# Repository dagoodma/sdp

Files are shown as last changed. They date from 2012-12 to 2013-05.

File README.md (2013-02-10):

                                                                          
         .oo          o                                                   
        .P 8          8                                                   
       .P  8 o    o  o8P .oPYo. odYo. .oPYo. ooYoYo. .oPYo. o    o .oPYo. 
      oPooo8 8    8   8  8    8 8' `8 8    8 8' 8  8 8    8 8    8 Yb..   
     .P    8 8    8   8  8    8 8   8 8    8 8  8  8 8    8 8    8   'Yb. 
    .P     8 `YooP'   8  `YooP' 8   8 `YooP' 8  8  8 `YooP' `YooP' `YooP' 
    ..:::::..:.....:::..::.....:..::..:.....:..:..:..:.....::.....::.....:
    ::::::::::::::::::::::::::::::::::::::::::::::::::::::::::::::::::::::
    ::::::::::::::::::::::::::::::::::::::::::::::::::::::::::::::::::::::
    
           o      o  d'b                                        8 
           8         8                                          8 
           8     o8 o8P  .oPYo. .oPYo. o    o .oPYo. oPYo. .oPYo8 
           8      8  8   8oooo8 8    8 8    8 .oooo8 8  `' 8    8 
           8      8  8   8.     8    8 8    8 8    8 8     8    8 
           8oooo  8  8   `Yooo' `YooP8 `YooP' `YooP8 8     `YooP' 
     ............:..:..:::.....::....8 :.....::.....:..:::::.....::.....::.
    ::::::::::::::::::::::::::::::ooP'.:::::::::::::::::::::::::::::::::::
    ::::::::::::::::::::::::::::::...:::::::::::::::::::::::::::::::::::'

Autonomous Lifeguard -- Senior Design Project for UCSC

*   Website: http://lifeguardrobotics.com
*   Source: https://github.com/dagoodma/sdp
*   Mailing list: [Google Groups](https://groups.google.com/a/ucsc.edu/forum/#!forum/albs-group)

This project consists of an autonomous surface vessel to aid a drowning
individual in the critical minutes that it takes a lifeguard to make it
out to a person. 

### License ###

The Autonomous Lifeguard project is proposed to be protected under either LGPL or GPLv3+.
See the *COPYING* file for more info.

### Credits ###

&copy; 2012-2013 [David Goodman](mailto:dagoodma@ucsc.edu),
 [Darrel Deo](mailto:ddeo@ucsc.edu),
 [Shehadeh Dajani](mailto:sdajani@ucsc.edu),
 [John Ash](mailto:jash@ucsc.edu)

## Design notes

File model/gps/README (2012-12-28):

Install drivers for FTDI, UART USB-Serial:
    http://www.ftdichip.com/FTDrivers.htm

Plug GPS devices in one at a time and record port names (*nix) or numbers
(windows) for each device. Enter these values into the portnums section
for each device in gps_autoconf.m

Run gps_autoconf.m is matlab. You will see:
    Connected to Locosys
    Connected to Mediatek
    Connected to Ublox
    Connected to San_Jose
    Connected to Sirf_Star

Use fscanf n matlab to print messages from a device. Locosys for example:
    > out = fscanf(ports{locosys})
    out =
    GGA,000525.836,,,,,0,0,,,M,,M,,*47
    > out = fscanf(ports{locosys})
    out =
    ...
    $GPRMC,000525.836,V,,,,,0.00,0.00,060180,,,N*4D
    $PMTK001,220,3*30
    $PMTK001,314,3*36
    $GPGGA,000526.836,,,,,0,0,,,M,,M,
    $GPRMC,000542.836,V,,,,,0.00,0.00,060180,,,N*4C
    $GPGGA,000527.836,,,,,0,0,,,M,,M,,*45
    $GPRMC,000527.836,V,,,,,0.00,0.00,060180,,,N*4F
    $GPGGA,000528.836,,,,,0,0,,,M,,M,,*4A

    Note that the above results were obtains when running the scripts indoors.

Verify timestamps at 1 Hz. See Messages for an explaination.

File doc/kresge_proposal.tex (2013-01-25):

 \documentclass[11pt]{article}
\usepackage[pdftex]{graphicx}
\usepackage{siunitx}
\usepackage{verbatim}
\usepackage{float}
\usepackage{lastpage}
\usepackage{fancyhdr}
\usepackage[margin=1in, paperwidth=8.5in, paperheight=11in]{geometry}
%\usepackage{indentfirst}

\newcommand{\HRule}{\rule{\linewidth}{0.5mm}}

% Header and Footer
\pagestyle{fancy}
%\fancyhead{} % clear all header fields
%\rhead{\vspace*{1em}\headone{David Goodman}\\
%	$118$ Hainline Road $\bullet$ Aptos, CA 95003\\
%	Phone: 714.363.1280\\
%	E-Mail: dagoodma@gmail.com}
%\cfoot{}

\renewcommand{\headrulewidth}{0pt}
%\renewcommand{\footrulewidth}{0.4pt}
%\cfoot{}
%\rfoot{Goodman \thepage}

\begin{document}

\begin{titlepage}
\begin{center}

% Upper part of the page. The '~' is needed because \\
% only works if a paragraph has started.
%\includegraphics[width=0.15\textwidth]{./logo}~\\[1cm]
\ \\[5.6cm]
\textsc{\LARGE \textbf{University of California, Santa Cruz} \\Baskin School of Engineering}\\[1.5cm]

\textsc{\Large Senior Design Project}\\[0.5cm]

% Title
\HRule \\[0.4cm]
{ \huge \bfseries Autonomous Lifeguard}\\[0.4cm]

\HRule \\[1.5cm]

% Author and supervisor
\begin{minipage}{0.4\textwidth}
\begin{flushleft} \large
\emph{Authors:}\\
Darrel \textsc{Deo}\\
David \textsc{Goodman}\\
John \textsc{Ash}\\
Shehadeh \textsc{Dajani}
\end{flushleft}
\end{minipage}
\begin{minipage}{0.4\textwidth}
\begin{flushright} \large
\emph{Advisors:} \\
Ph.D. ~Gabriel \textsc{Elkaim}\\
Ph.D. ~John \textsc{Vesecky}\\
Ph.D. ~Stephen \textsc{Petersen}
\end{flushright}
\end{minipage}

\vfill

% Bottom of the page
{\large \today}

\end{center}
\end{titlepage}

\section*{Abstract}
In the United States, there have been a reported 99 people that have drowned in the past year alone, with a good number of them occurring while a lifeguard was on duty. In that year, there were 63,000 individual cases where Lifeguards rescued people at risk of drowning. We are proposing an autonomous surface vehicle to aid and assist these drowning individuals during the critical minutes before help can reach them.\\

Our project allows a lifeguard to quickly target a drowning person with a magnifying scope that will obtain their GPS coordinates and communicate them to a boat located in the water beyond the shore break. The boat will autonomously navigate to the person, allowing them to hang on and stay afloat until the lifeguard arrives. This project aims to keep beaches safer by reducing the risk of drowning. 

\section*{Narrative}

\subsection*{Background}
The city of Los Angeles has employed the use of a device named EMILY (Emergency Integrated Lifesaving Lanyard) on their state beaches to save drowning victims. The device is deployed from the shore and remotely controlled by a human operator. Although it offers a degree of assistance, there exist multiple drawbacks to the system as a whole. The first is that it requires an operator, meaning that a lifeguard will be occupied with controlling the device during a rescue. The second is that the device must fight against the waves in order to reach the victim. This implies an unpredictable delay when navigating to the victim. The third drawback is that the device is limited by the field of view and skill of the operator.\\

We propose a fully autonomous system that will navigate to the location of a drowning victim, offering assistance as a lifeguard is deployed from shore. This eliminates the need for a human operator, allowing the lifeguard to swim out to the victim as the device navigates to the victim. The device will be stationed within the water at a certain distance from the shore and beyond the wave breaks so that it may arrive at a drowning victim's location swiftly.

\subsection*{Objective}

Motivated by the number of drowning cases each year, The Autonomous Lifeguard Senior Design Group aims to develop an assistive, life-preserving, vessel with the capability of navigating to and locating drowning individuals in open water. This vessel, the Autonomous Lifeguard Assistant (AtLAs), will be stationed in the open water on a beach or in a lake. The AtLAs will be coupled with an onshore control tower, the Command Post Acquisition System (ComPAS), that transmits the GPS coordinates of drowning individuals that have been spotted by a lifeguard. While the lifeguard swims to the drowning individual, the AtLAs will use its triple motor propulsion system to arrive at the victim's location at least three times as fast as a lifeguard can. Furthermore, the entire Autonomous Lifeguard System is designed to be a useful and affordable product for the public. The ultimate goal is to create a practical and superior aquatic life-saving system.

\subsection*{Procedure}
This project is composed of two systems, a command center (ComPAS) and Autonomous Lifeguard Assistant (AtLAs), which will communicate with each other over a wireless protocol. The ComPAS consists of a GPS-equipped scope mounted on a lifeguard post. When the lifeguard sees someone who is drowning, he or she will spot them through the scope and press a button. At that instant, the coordinate location of the victim will be obtained--through triangulation algorithms and a global coordinate system provided by the GPS--and sent to the AtLAs in the water. The AtLAs will then begin to self navigate to the location using its own on-board GPS device as well as an array of sensors for detecting the person. Upon reaching this destination, the AtLAs will intelligently traverse the area until it finds the drowning victim. The AtLAs will support the victim and allow them to rest while the lifeguard makes their way out.\\

In order to accomplish our objective, we propose a three phase approach: design, integration, and testing. In the design stage, which we are currently in, a majority of the research was accomplished to establish a solution to the task and physical and mathematical models were created to allow for an enlightened analysis of the proposed solution. Next, the models established in the design phase are to be rigorously examined in the testing phase to acquire real data to prove the accuracy and robustness of the model. Lastly, the integration stage, in which the minimum specifications will be addressed, involves assembling the final product by combining all the refined modules into a physical implementation that meets the specifications. These three phases encompass the life of the project. \\

Since mid-November, our team has made significant progress in completing the research and design phase for our project. We began by doing extensive background research related to the sensors and actuators, as well as the basic physical capabilities required. This led to modeling and physical calculation related to the buoyancy, hydrodynamics, motors, power budget, sensor specifications, and the accuracy of our navigation system. Using this research, we formulated various initial solutions, and then, with the input of trusted and qualified mentors, proceeded to amend, revise, and ultimately converge onto an effective solution. Next, we completed a group charter, an itemized budget, a Gantt chart, a project proposal, and have already given two presentations to audiences composed of engineering professors and students. In order to complete the design stage, we are in the process of designing physical prototypes of the ComPAS and the AtLAs and have already ordered and received a majority of the sensors we will be using. This first stage is nearly complete, and once we are done we will be ready to integrate our prototypes into a cohesive product.\\

The next phase is integration. In the integration phase, we will be combining the working prototypes from the design phase into a complete product. This will involve finalizing the ComPAS and improving its robustness for transportation to the test location. The AtLAs will also need to be assembled and finalized, outfitted with buoyancy foam and protective boat fenders, and cleared for use in lakes and oceans. Also, we will need to reinforce both the AtLAs and the ComPAS and ensure that they are properly waterproofed and protected against the elements. Once the integration of our systems is complete, we can begin testing and assessing the performance of the systems.\\

The testing phase is the third and final stage. It includes a thorough investigation of our assembled systems and their ability to meet the established objectives. Unit tests have been created that will help streamline this process and prevent fixes from being introduced that adversely affect another piece of the system without being detected. As a final test, we will place the ComPAS on the shore of a lake or beach in Santa Cruz, deploy the AtLAs from the water, and then use the ComPAS and AtLAs to save a "drowning" volunteer. Once our system passes this minimum specification we will have completed our project.

\subsection*{Qualifications}

Darrel Deo is our team leader. He will also be working on integrating the sensors and building the tripod, which will be used to obtain the GPS coordinates of the drowning victim. Darrel is qualified for this position because of his work at MIT. While at MIT, Darrel worked with the Robotics, Vision, and Sensor Networks Group (RVSN) where he helped develop an assistive device for the visually impaired. This experience makes him well qualified for leading our team, and handling the sensor integration for the project.\\

Shehadeh Dajani is managing our budget. He will also be leading our Printed Circuit Board (PCB) design and layout, along with our vehicle design. Shehadeh is qualified for these positions because he has taken a course on PCB design and designed numerous PCBs both educationally and industrially. Shehadeh has also had previous experience with ROVs, at the University of Maryland. Finally, Shehadeh will be heading the human detection portion of the project by working with Darrel to design and modify existing sensors for aquatic human detection.\\

John Ash is managing our schedule for the project. He will also be working on the wireless protocols, water proofing, and PCB fabrication. John is qualified for these positions because of his previous experience with point-to-point communications. His experience with the autonomous solar boat on campus in the Autonomous Systems Lab (ASL) makes him an excellent consultant for protecting our hardware from water. Furthermore, John has hands-on experience fabricating PCBs.\\

David Goodman is our document administrator. He will also be developing the Finite State Machine (FSM) for our robot and the navigation system. David is more than qualified for this position, because he has five years of software engineering experience in industry. He is able to oversee design and testing of the software portion of our project. David has also worked in the ASL on the boat project, and with a graduate student on GPS-related research for the lab. David has the necessary experience to head the design and implementation of the software navigation system for our project.

\subsection*{Benefits}

This project will directly benefit the Santa Cruz community, as well as any coastal community around the world, by assisting a lifeguard to be more effective at saving people from drowning. Furthermore, the target budget for the Autonomous Lifeguard System, including research, is aimed at making this project a sensible and affordable end product that has the real opportunity to be used. The project is established in a way to allow for expansion from the original scope so that the AtLAs can be used for search and rescue or patrolling situations. Overall, we plan on using our engineering skills and talents to design a product with the sole purpose of saving lives and reducing the risk of drowning across the globe.

\end{document}

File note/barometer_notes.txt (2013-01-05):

Barometric Pressure Sensor - BMP085 Breakout (sparkfun)
https://www.sparkfun.com/products/9694

digital pressure sensor by Bosch
range: +9000m .. -500m above sea level
features: temperature, I2C, calibrated, MSL 1

piezo resistive sensor
data: pressure (16-19 bits), temp. (16 bits)

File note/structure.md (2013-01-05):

Repository Structure
====================

* _doc_ - Documentation, datasheets, schematics, and images.
* _include_ - Header files for project source code.
* _model_ - MATLAB models and data.
* _note_ - Notes, guides, tutorials, research.
* _src_ - C source code files.
* _t_ - Unit tests and harnesses.
* _tool_ - Tools and utilities.
* _example_ - Example code.

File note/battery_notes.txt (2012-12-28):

LiPo RC battery pack voltages
--
3.7 volt battery = 1 cell x 3.7 volts (1S)
7.4 volt battery = 2 cells x 3.7 volts (2S)
11.1 volt battery = 3 cells x 3.7 volts (3S)
14.8 volt battery = 4 cells x 3.7 volts (4S)
18.5 volt battery = 5 cells x 3.7 volts (5S)
22.2 volt battery = 6 cells x 3.7 volts (6S)
29.6 volt battery = 8 cells x 3.7 volts (8S)
37.0 volt battery = 10 cells x 3.7 volts (10S)
44.4 volt battery = 12 cells x 3.7 volts (12S)

http://www.rchelicopterfun.com/rc-lipo-batteries.html

http://www.hobbyking.com/hobbyking/store/__14616__Turnigy_nano_tech_5000mah_6S_45_90C_Lipo_Pack.html

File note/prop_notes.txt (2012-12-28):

Notes:
--
Rule of thumb: 2" pitch = 400 RPM

Definitions:
--

Pitch: theoretical distance the prop travels on each rotation. This is theoretical because water is not a solid medium and the prop slips. 10 to 30% is normal, the lower numbers are found only on hi-performance props, specially prepared. 

Transom = stern = rear = aft-most 

http://www.modelpowerboat.com/content.php?152-RC-Model-Boat-Propellers

http://boatpropellers.iboats.com/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

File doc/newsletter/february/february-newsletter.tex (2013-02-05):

%%% LaTeX Template: Newsletter
%%%
%%% Source: http://www.howtotex.com/
%%% Feel free to distribute this template, but please keep the referal to HowToTeX.com.
%%% Date: September 2011

%%% ---------------
%%% PREAMBLE
%%% ---------------
\documentclass[10pt,a4paper]{article}

% Define geometry (without using the geometry package)
\setlength\topmargin{-48pt}
\setlength\headheight{0pt}
\setlength\headsep{25pt}
\setlength\marginparwidth{-20pt}
\setlength\textwidth{7.0in}
\setlength\textheight{9.5in}
\setlength\oddsidemargin{-30pt}
\setlength\evensidemargin{-30pt}

\frenchspacing						% better looking spacing

% Call packages we'll need
\usepackage[english]{babel}			% english
\usepackage{graphicx}				% images
\usepackage{amssymb,amsmath}		% math
\usepackage{multicol}				% three-column layout
\usepackage{url}					% clickable links
\usepackage{marvosym}				% symbols
\usepackage{wrapfig}				% wrapping text around figures
\usepackage[T1]{fontenc}			% font encoding
\usepackage{charter} 				% Charter font for main content
\usepackage{blindtext}				% dummy text
\usepackage{datetime}				% custom date
	\newdateformat{mydate}{\monthname[\THEMONTH] \THEYEAR}
\usepackage[pdfpagemode=FullScreen,
			colorlinks=false]{hyperref}	% links and pdf behaviour

% Customize (header and) footer
\usepackage{fancyhdr}
\pagestyle{fancy}
\lfoot{	\footnotesize 
		Newletter from LifeguardRobotics.com \\
		\Mundus\ \href{http://www.lifeguardrobotics.com}{LifeguardRobotics.com}	\quad
		\Telefon\ (831) 704-6771										\quad
		\Letter\ \href{mailto:lifeguardrobotics@gmail.com}{lifeguardrobotics@gmail.com}
	  }
\cfoot{}
\rfoot{\footnotesize ~\\ Page \thepage}
\renewcommand{\headrulewidth}{0.0pt}	% no bar on top of page
\renewcommand{\footrulewidth}{0.4pt}	% bar on bottom of page

%%% ---------------
%%% DEFINITIONS
%%% ---------------

% Define separators
\newcommand{\HorRule}[1]{\noindent\rule{\linewidth}{#1}} % Creating a horizontal rule
\newcommand{\SepRule}{\noindent							 % Creating a separator
						\begin{center}
							\rule{250pt}{1pt}
						\end{center}
						}						

% Define Title en News input
\newcommand{\JournalName}[1]{%
		\begin{center}	
			%\Huge \usefont{T1}{augie}{m}{n}
			\Huge \usefont{T1}{cmr}{m}{n}
			%\huge \bfseries 
			#1%
		\end{center}	
		\par \normalsize \normalfont}
		
\newcommand{\JournalIssue}[1]{%
		\hfill \textsc{\mydate \today, No #1}
		\par \normalsize \normalfont}

\newcommand{\NewsItem}[1]{%
		\usefont{T1}{augie}{m}{n} 	
		\large #1 \vspace{4pt}
		\par \normalsize \normalfont}
		
\newcommand{\NewsAuthor}[1]{%
			\hfill by \textsc{#1} \vspace{4pt}
			\par \normalfont}		

%%% ---------------
%%% BEGIN DOCUMENT
%%% ---------------
\begin{document}
% Title	
% -----
\JournalIssue{1}
\JournalName{The Autonomous Lifeguard Project}
\noindent\HorRule{3pt} \\[-0.75\baselineskip]
\HorRule{1pt}
% -----

% Front article
% -----
\vspace{0.5cm}
	\SepRule
\vspace{0.5cm}

\begin{center}
\begin{minipage}[h]{0.80\linewidth}
	\begin{wrapfigure}{l}{0.415\textwidth}
		{%
		\setlength{\fboxsep}{0pt}%
		\setlength{\fboxrule}{1pt}%
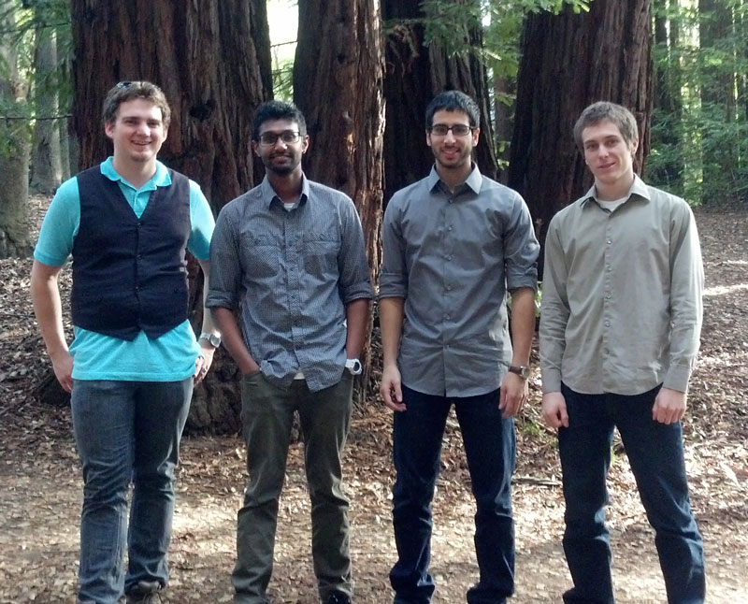
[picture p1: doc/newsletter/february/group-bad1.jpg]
		\fbox{}%
		}%
		%\\	% this spacer is needed to make the text on the right fit OK
	\end{wrapfigure}
	
	\NewsItem{Who Are We}
	\emph{We are a group of UC Santa Cruz computer and robotics engineering students who are building a robot to assist lifeguards in saving drowning individuals on beaches, at sea, and in other bodies of water. In the United States, there has been a reported 99 people that have drowned in the past year alone, with a good number of them occurring while a lifeguard was on duty. We propose an autonomous boat that can navigate to a person, allowing them to hang on and stay a float until the lifeguard arrives. Our aim is to keep beaches safer by reducing the risk of drowning.}
\end{minipage}
\end{center}
% -----

% Other news (1)
% -----
\vspace{0.5cm}
	\SepRule
\vspace{0.5cm}
\begin{multicols}{3}
	\NewsItem{Progress}
	\NewsAuthor{D. Goodman}
	January has been a very productive month for our team. We are making substantial progress on the project. Throughout January, we have been hard at work writing, researching, coding, and soldering. Administratively, we have completed a Gantt chart, a website, and have entered into the Texas Instruments Analog Design Contest. In the hardware portion, we have purchased a boat and begun to modify it with new motors, electronic speed controllers, and batteries.  The command center---an encoded tripod assembly that the lifeguard will use to designate a drowning person---is coming together as well. We have acquired a tripod and absolute rotary encoders for triangulation. The encoder housing has been created, and a software interface is now in the works to take angular measurements and translate them into distance. Great care has been taken to ensure that the encoders are very precise so that we can triangulate the position of a drowning person accurately with minimal error. Many of our other sensors are nearly complete as well. We have an accelerometer up and running, our thermal imagining nearly complete, our altimeter is working, our GPSs running and we are analyzing their data in MATLAB, and we have been planning our approach to implementing the microwave radar and sonar sensors after inspecting their analog waveforms with an oscilloscope. 
\begin{center}
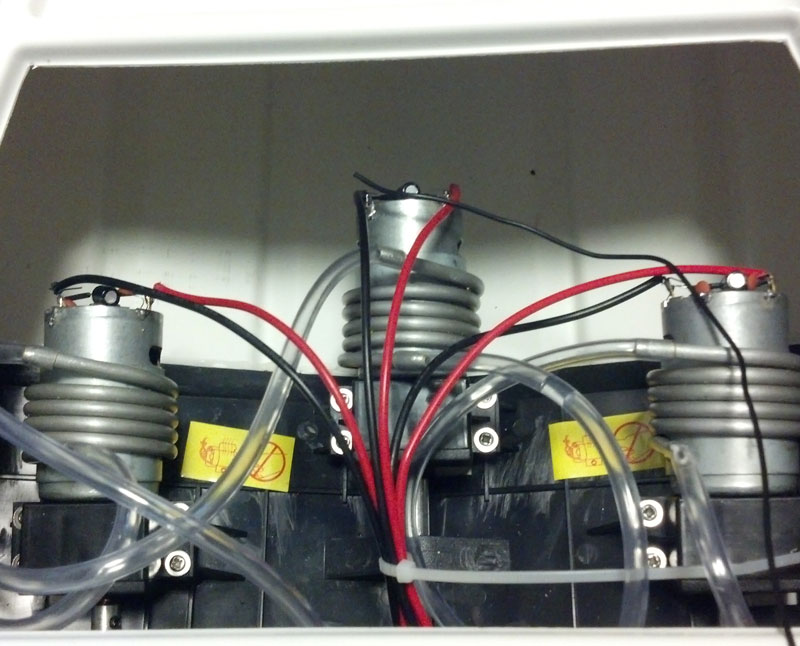
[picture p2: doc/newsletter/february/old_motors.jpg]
			
		\end{center}
Overall, this past month has been productive on all fronts and the team is anxious to continue with work in February.
		
% -----

\vspace{1cm}
% Other news (2)
% -----
\NewsItem{Direction}
\NewsAuthor{D. Deo}
	Every week, the team specifies a minimum set of personal goals that they wish to complete.
 This week the group will focus on modeling accurate data from the encoders, XBee, GPS, and thermal sensor. The goal is to get the encoders to read accurate angles and have the ability to be calibrated to a zero degree point within software. Data from the GPS and XBee need to be obtained over a duration of time to analyze and correct for any error that may be present. The thermal sensor data is to be mapped to an RGB array so that heat signatures may be seen in real time. These sensors and modules are the last that need be implemented before the integration phase where the various components will be mounted on their respective subsystem. Comprehensive testing will occur after each sensor is up and running. We will also begin designing hierarchical finite state machines for the boat and the command center. These will provide our systems with the intelligence to act autonomously and make decisions on its own. So far, we are ahead of schedule for February.

% -----
%\columnbreak
\vspace{1cm}
% Other news (2)
% -----
\NewsItem{Support}
\NewsAuthor{D. Deo}
The Autonomous Lifeguard Group is moving quite swiftly and is hopeful that the next phases of the project will yield exceptional results. As a devoted team, we are currently funding the project entirely ourselves. Optimistic about the future of the Autonomous Lifeguard Project, we would appreciate any form of support that would help the project advance. Donations are welcome and can be submitted via our website. All considerations will be recognized by the team.
\end{multicols}
% -----
\end{document}

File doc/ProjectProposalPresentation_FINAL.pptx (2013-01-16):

## Autonomous Lifeguard

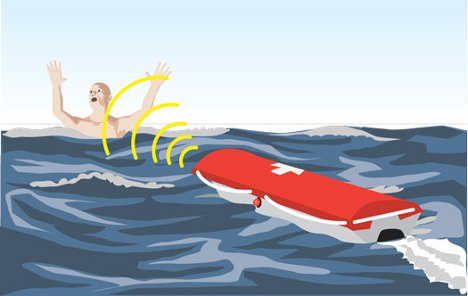
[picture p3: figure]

- Darrel R. Deo (Project Lead)
- Shehadeh H. Dajani
- John P. Ash
- David A. Goodman
- University of California at Santa Cruz

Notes: Hello, We are the autonomous Lifeguard group, My name is …, I am a … year … Engineer. Hello my name is ...... I am a ..... with a focus in ......

## Mission Statement

- Autonomous surface vessel (ASV) to aid and assist drowning victims.
- 2-part system:
  - Command Center
  - ASV

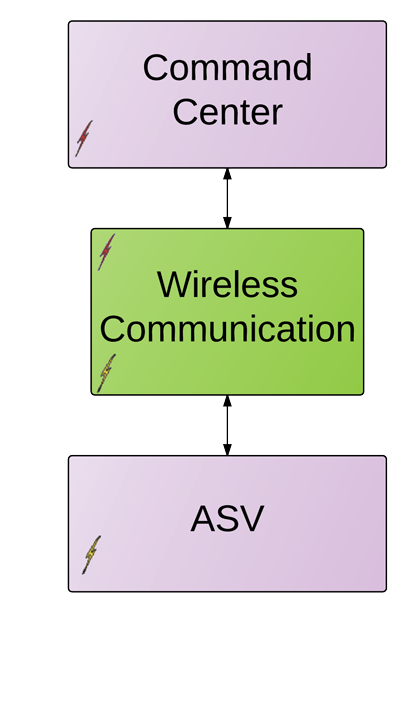
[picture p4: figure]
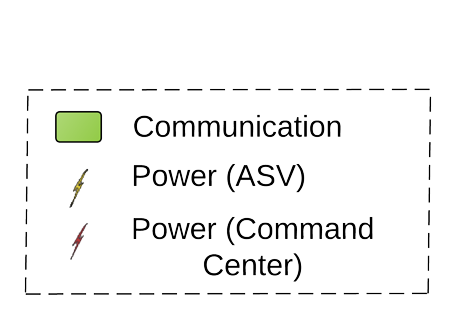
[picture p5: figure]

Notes: We are proposing an autonomous surface vehicle to aid a drowning individual in the critical minutes that it takes a lifeguard to make it out to a person.

We are interested in the case beyond the breaks where it would take a lifeguard a while to make it out to the person.

Our system is composed of two subsystems

## Motivation

- Santa Cruz - “Surf City”
- E.M.I.L.Y - Emergency Integrated Lifesaving Lanyard
      - Remote controlled
      - Deployed from beach
      - Non-practical

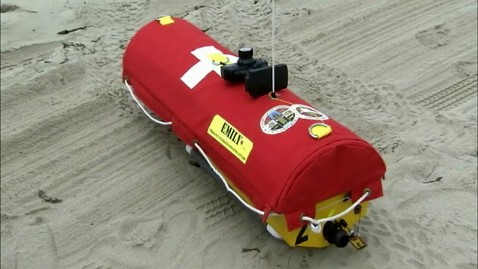
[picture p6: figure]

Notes: range is

## Objective

Develop a system that will aid drowning victims.

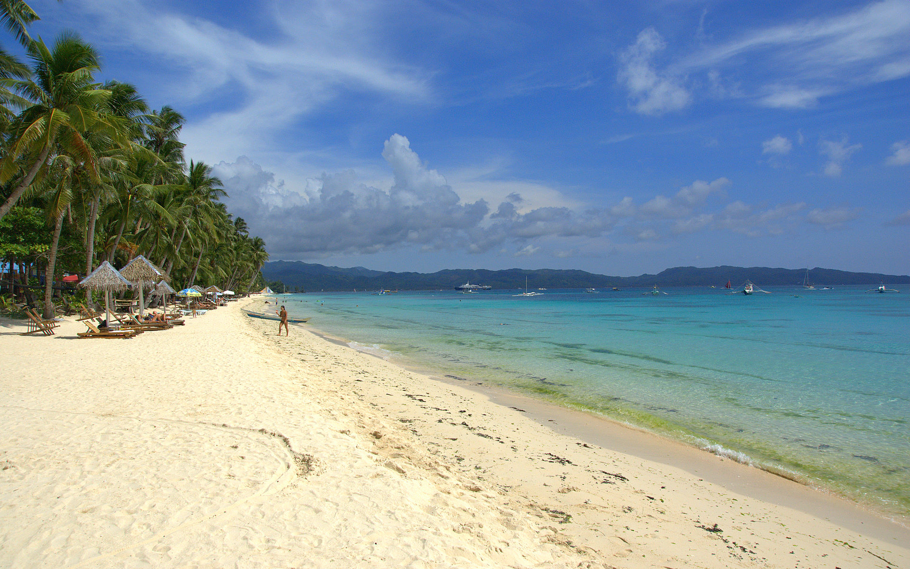
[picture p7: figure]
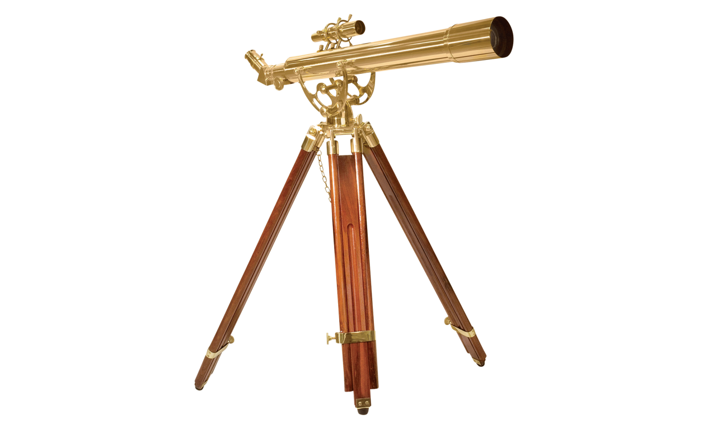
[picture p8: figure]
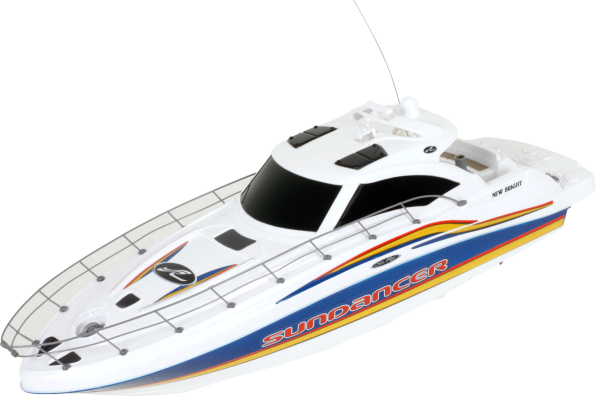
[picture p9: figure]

## Scope of Specifications

  - Range of rescue will be from beyond surf breaks to 600ft.
  - ASV will be anchored at a specified waypoint in the water.
  - Command Center will be located on a lifeguard post.
  - Both subsystems will communicate via wireless protocol.

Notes: Range: It will take the average swimmer to swim up to 600 ft, at which point a lifeguard will be able to swim out in 5 minutes.

## Minimum Functionality

- Command Center
  - Obtain the drowning victim’s location within +/- 50 ft.
  - Required to send wireless information at least 600 ft.
  - Must have an override remote control function allowing full control of ASV.

## Minimum Functionality

- Autonomous Surface Vehicle:
  - Speed of ASV must, at least, double that of a lifeguard’s swim speed (3.7 MPH).
  - Batteries must last for at least 12 hours without recharge.
  - Must be able to navigate to a specified GPS coordinate within +/- 20 ft.

## Differential GPS

- Calibrate reference station position average over time
- Calculate instantaneous GPS error
- Transmit error to rover for corrections
- 1.1cm to 3.2ft of accuracy achieved

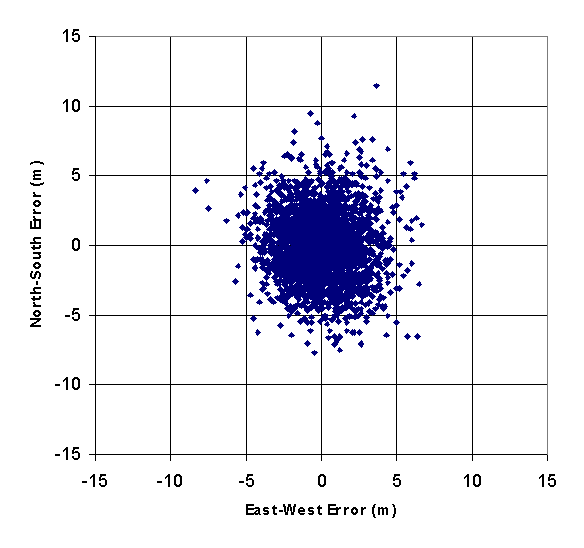
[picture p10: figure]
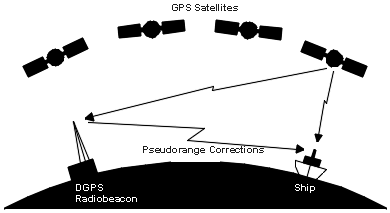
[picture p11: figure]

## Encoder Accuracy

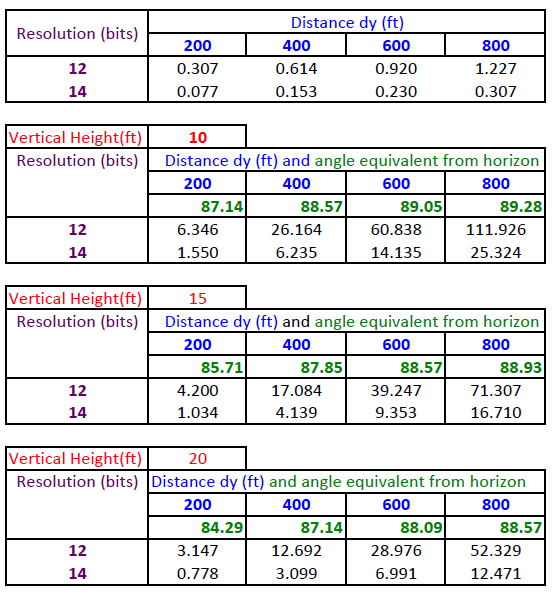
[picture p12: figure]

## Block Diagram

- Command Center

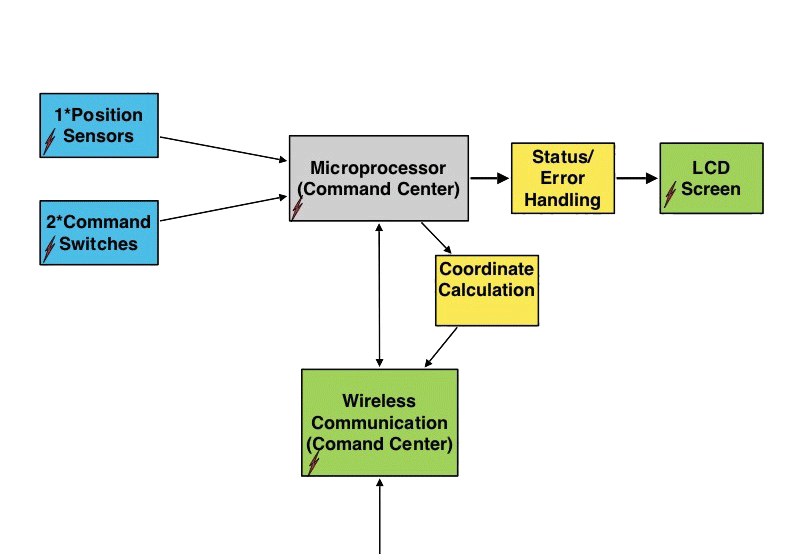
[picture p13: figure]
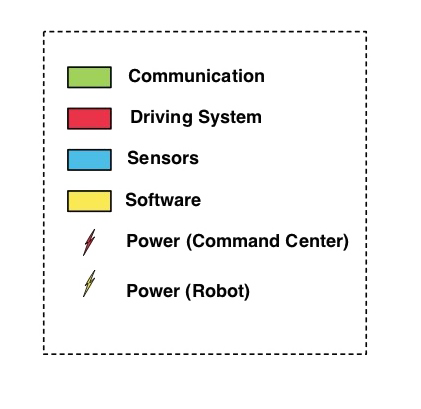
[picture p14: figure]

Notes: Add sensor blocks
Switches can be put into interface sensors

## Block Diagram

- ASV

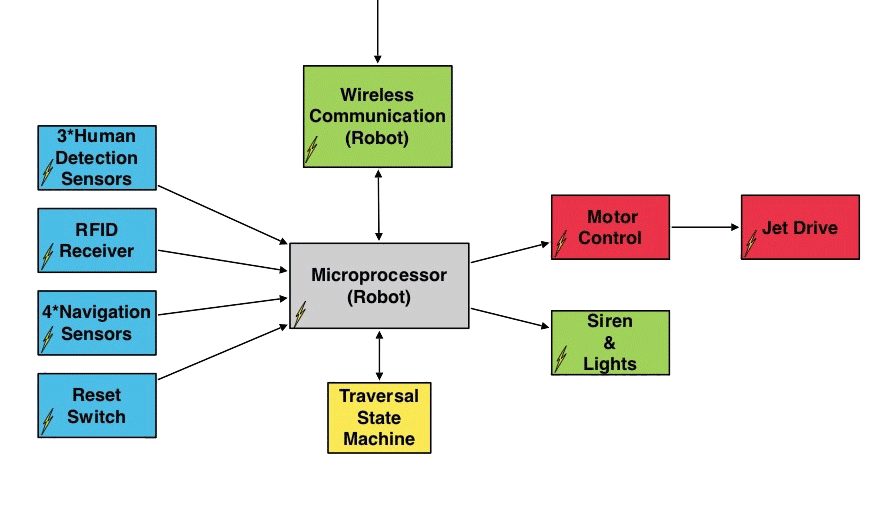
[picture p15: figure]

## Division of Labor

- John Ash – Schedule Planner
      - Wireless Protocol, Power Management, PCB Routing
- Shehadeh Dajani – Budget Coordinator
      - Motor Control, PCB Design/Layout, Vehicle Design
- Darrel Deo – Team Leader
      - Sensor Integration, Tripod Design, Modeling
- David Goodman - Document Administrator
      - Software Test Harnesses, FSM Design, GPS Integration

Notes: John: qualifications: XBee experience (121 expansion), autonomous boat for ASL,
David: software eng. for 5yrs industry exp., DSP, and GPS (ASL)
Shehadeh: Quals: Mechatronics motor control, solidworks fiend, board layout exp.
Darrel : Quals: Sensor Technology experience, math modeling--Solid Mechanics

## Gantt Chart

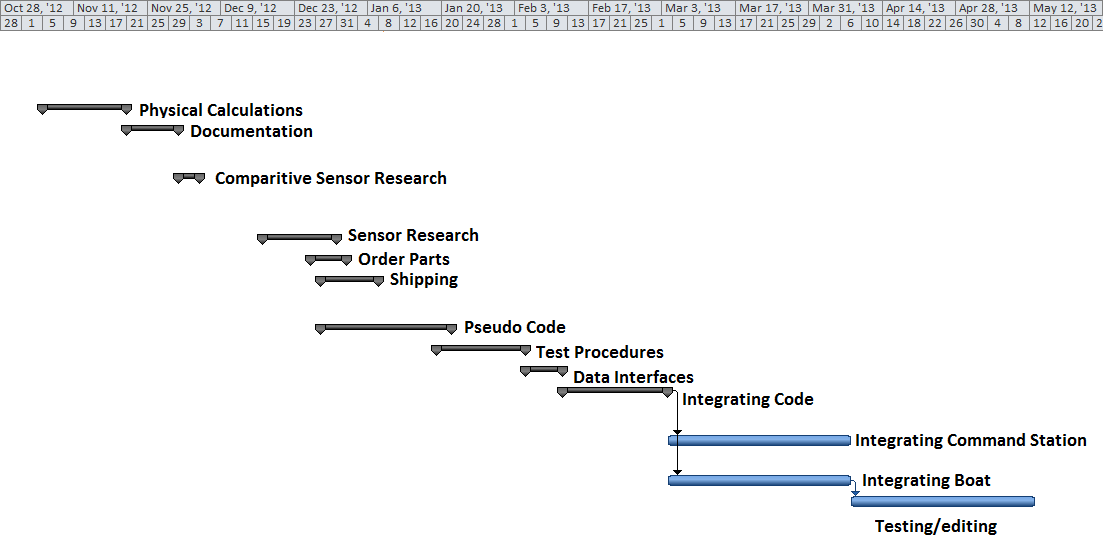
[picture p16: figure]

## Itemized Budget

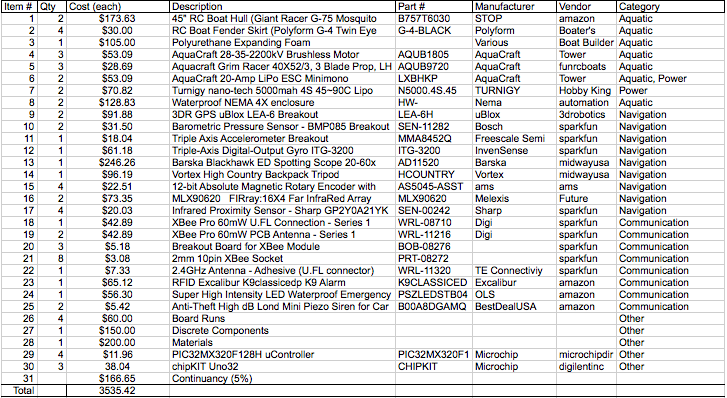
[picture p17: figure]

## Progress

- Boat Hull has been ordered and is in route.
- Started extracting coordinate data from GPS devices.
- Established Xbee communication.
- Beginning to interface decoder wheels with Micro.
- Currently seeking funding sources (Kresge, Oakes, Crown, and Corporations.)

## Conclusion

- All team members are proficient in their field of responsibility.
- Gabriel Elkaim has shown support and offered mentorship.
- We have access to field testing environments (e.g. pool, lake, ocean).
- This project has the real potential to be an asset to lifeguards and save lives.
- Marketable to beaches across the country.

## References

- EMILY:
  - http://www.popsci.com/gadgets/article/2010-06/invention-month-robot-lifeguard

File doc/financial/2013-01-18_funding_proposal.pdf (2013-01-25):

## University of California, Santa Cruz

Baskin School of Engineering

Senior Design Project

# Autonomous Lifeguard

Authors:
Darrel Deo
David Goodman
John Ash
Shehadeh Dajani

Advisors:
Ph.D. Gabriel Elkaim
Ph.D. John Vesecky
Ph.D. Stephen Petersen

January 18, 2013

## Abstract

In the United States, there have been a reported 99 people that have drowned in the past year alone, with a good number of them occurring while a lifeguard was on duty. In that year, there were 63,000 individual cases where Lifeguards rescued people at risk of drowning. We are proposing an autonomous surface vehicle to aid and assist these drowning individuals during the critical minutes before help can reach them.

Our project allows a lifeguard to quickly target a drowning person with a magnifying scope that will obtain their GPS coordinates and communicate them to a boat located in the water beyond the shore break. The boat will autonomously navigate to the person, allowing them to hang on and stay afloat until the lifeguard arrives. This project aims to keep beaches safer by reducing the risk of drowning.

## Narrative

Background

The city of Los Angeles has employed the use of a device named EMILY (Emergency Integrated Lifesaving Lanyard) on their state beaches to save drowning victims. The device is deployed from the shore and remotely controlled by a human operator. Although it offers a degree of assistance, there exist multiple drawbacks to the system as a whole. The first is that it requires an operator, meaning that a lifeguard will be occupied with controlling the device during a rescue. The second is that the device must fight against the waves in order to reach the victim. This implies an unpredictable delay when navigating to the victim. The third drawback is that the device is limited by the field of view and skill of the operator.

We propose a fully autonomous system that will navigate to the location of a drowning victim, offering assistance as a lifeguard is deployed from shore. This eliminates the need for a human operator, allowing the lifeguard to swim out to the victim as the device navigates to the victim. The device will be stationed within the water at a certain distance from the shore and beyond the wave breaks so that it may arrive at a drowning victim’s location swiftly.

Objective

Motivated by the number of drowning cases each year, The Autonomous Lifeguard Senior Design Group aims to develop an assistive, life-preserving, vessel with the capability of navigating to and locating drowning individuals in open water. This vessel, the Autonomous Lifeguard Assistant (AtLAs), will be stationed in the open water on a beach or in a lake. The AtLAs will be coupled with an onshore control tower, the Command Post Acquisition System (ComPAS), that transmits the GPS coordinates of drowning individuals that have been spotted by a lifeguard. While the lifeguard swims to the drowning individual, the AtLAs will use its triple motor propulsion system to arrive at the victim’s location at least three times as fast as a lifeguard can. Furthermore, the entire Autonomous Lifeguard System is designed to be a useful and affordable product for the public. The ultimate goal is to create a practical and superior aquatic life-saving system.

Procedure

This project is composed of two systems, a command center (ComPAS) and Autonomous Lifeguard Assistant (AtLAs), which will communicate with each other over a wireless protocol. The ComPAS consists of a GPS-equipped scope mounted on a lifeguard post. When the lifeguard sees someone who is drowning, he or she will spot them through the scope and press a button. At that instant, the coordinate location of the victim will be obtained–through triangulation algorithms and a global coordinate system provided by the GPS–and sent to the AtLAs in the water. The AtLAs will then begin to self navigate to the location using its own on-board GPS device as well as an array of sensors for detecting the person. Upon reaching this destination, the AtLAs will intelligently traverse the area until it finds the drowning victim. The AtLAs will support the victim and allow them to rest while the lifeguard makes their way out.

In order to accomplish our objective, we propose a three phase approach: design, integration, and testing. In the design stage, which we are currently in, a majority of the research was accomplished to establish a solution to the task and physical and mathematical models were created to allow for an enlightened analysis of the proposed solution. Next, the models established in the design phase are to be rigorously examined in the testing phase to acquire real data to prove the accuracy and robustness of the model. Lastly, the integration stage, in which the minimum specifications will be addressed, involves assembling the final product by combining all the refined modules into a physical implementation that meets the specifications. These three phases encompass the life of the project.

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

The next phase is integration. In the integration phase, we will be combining the working prototypes from the design phase into a complete product. This will involve finalizing the ComPAS and improving its robustness for transportation to the test location. The AtLAs will also need to be assembled and finalized, outfitted with buoyancy foam and protective boat fenders, and cleared for use in lakes and oceans. Also, we will need to reinforce both the AtLAs and the ComPAS and ensure that they are properly waterproofed and protected against the elements. Once the integration of our systems is complete, we can begin testing and assessing the performance of the systems.

The testing phase is the third and final stage. It includes a thorough investigation of our assembled systems and their ability to meet the established objectives. Unit tests have been created that will help streamline this process and prevent fixes from being introduced that adversely affect another piece of the system without being detected. As a final test, we will place the ComPAS on the shore of a lake or beach in Santa Cruz, deploy the AtLAs from the water, and then use the ComPAS and AtLAs to save a ”drowning” volunteer. Once our system passes this minimum specification we will have completed our project.

Qualifications

Darrel Deo is our team leader. He will also be working on integrating the sensors and building the tripod, which will be used to obtain the GPS coordinates of the drowning victim. Darrel is qualified for this position because of his work at MIT. While at MIT, Darrel worked with the Robotics, Vision, and Sensor Networks Group (RVSN) where he helped develop an assistive device for the visually impaired. This experience makes him well qualified for leading our team, and handling the sensor integration for the project.

Shehadeh Dajani is managing our budget. He will also be leading our Printed Circuit Board (PCB) design and layout, along with our vehicle design. Shehadeh is qualified for these positions because he has taken a course on PCB design and designed numerous PCBs both educationally and industrially. Shehadeh has also had previous experience with ROVs, at the University of Maryland. Finally, Shehadeh will be heading the human detection portion of the project by working with Darrel to design and modify existing sensors for aquatic human detection.

John Ash is managing our schedule for the project. He will also be working on the wireless protocols, water proofing, and PCB fabrication. John is qualified for these positions because of his previous experience with point-to-point communications. His experience with the autonomous solar boat on campus in the Autonomous Systems Lab (ASL) makes him an excellent consultant for protecting our hardware from water. Furthermore, John has hands-on experience fabricating PCBs.

David Goodman is our document administrator. He will also be developing the Finite State Machine (FSM) for our robot and the navigation system. David is more than qualified for this position, because he has five years of software engineering experience in industry. He is able to oversee design and testing of the software portion of our project. David has also worked in the ASL on the boat project, and with a graduate student on GPS-related research for the lab. David has the necessary experience to head the design and implementation of the software navigation system for our project.

Benefits

This project will directly benefit the Santa Cruz community, as well as any coastal community around the world, by assisting a lifeguard to be more effective at saving people from drowning. Furthermore, the target budget for the Autonomous Lifeguard System, including research, is aimed at making this project a sensible and affordable end product that has the real opportunity to be used. The project is established in a way to allow for expansion from the original scope so that the AtLAs can be used for search and rescue or patrolling situations. Overall, we plan on using our engineering skills and talents to design a product with the sole purpose of saving lives and reducing the risk of drowning across the globe.

## Autonomous Lifeguard Project

### Itemized Budget

Item # | Qty | Cost (each) | Description | Part # | Manufactu rer | Vendor | Category | Notes
1 | 2 | $173.63 | 45" RC Boat Hull (Giant Racer G-75 Mosquito Craft) | B757T6030 | STOP | amazon | Aquatic | Going to test, then possibly modify or return.
2 | 4 | $30.00 | RC Boat Fender Skirt (Polyform G-4 Twin Eye Fender 6.5 x 23 - Black w/Air Adapter) | G-4-BLACK | Polyform | Boater's Marine Supply | Aquatic
3 | 1 | $105.00 | Polyurethane Expanding Foam (2 gal kit 50/50 mix) | | Various | Boat Builder Central | Aquatic | 480 lbs of buoyancy U.S. Coast Guard Approved
4 | 3 | $53.09 | AquaCraft 28-35-2200kV Brushless Motor MiniMono | AQUB1805 | AquaCraft | Tower Hobbies | Aquatic
5 | 3 | $28.69 | Aquacraft Grim Racer 40X52/3, 3 Blade Prop, LH | AQUB9720 | AquaCraft | funrcboats | Aquatic | 40mm (1.57") x 52MM Pitch. Copper-Beryllium-Titanium. Must hand finish.
6 | 2 | $53.09 | AquaCraft 20-Amp LiPo ESC Minimono | LXBHKP | AquaCraft | Tower Hobbies | Aquatic, Power | 20 Amp
7 | 2 | $70.82 | Turnigy nano-tech 5000mah 4S 45~90C Lipo Battery Pack | N5000.4S.45 | TURNIGY | Hobby King | Power | 5000mAh, 4 Cell (14.8V), 45C Constant / 90C Burst
8 | 2 | $128.83 | Waterproof NEMA 4X enclosure | HW-J161406SC | Nema | automatio ndirect | Aquatic | 4SCREWS OPQ CVR GRY 4X 16X14X6IN
9 | 2 | $91.88 | 3DR GPS uBlox LEA-6 Breakout | LEA-6H | uBlox | 3drobotics | Navigation | UART, USB interfaces. Includes ceramic antenna, LNA, SAW filter, and 3.3V batt.
10 | 2 | $31.50 | Barometric Pressure Sensor - BMP085 Breakout | SEN-11282 | Bosch | sparkfun | Navigation | I2C interface. Piezoelectric, includes temp. sensor.
11 | 1 | $18.04 | Triple Axis Accelerometer Breakout | MMA8452Q | Freescale Semi | sparkfun | Navigation | I2C interface. 3-axis, 2 ISR pins, optional HPF.
12 | 1 | $61.18 | Triple-Axis Digital-Output Gyro ITG-3200 Breakout | ITG-3200 | InvenSens e | sparkfun | Navigation | I2C interface. 3-axis, optional LPF, and ISR pin.
13 | 1 | $246.26 | Barska Blackhawk ED Spotting Scope 20-60x 60mm Angled Body | AD11520 | Barska | midwayus a | Navigation | Great at 600-800ft. 60mm, 20-60x.
14 | 1 | $96.19 | Vortex High Country Backpack Tripod | HCOUNTRY | Vortex | midwayus a | Navigation | Full size, 4.48 ft tall, 2.1 lbs.
15 | 4 | $22.51 | 12-bit Absolute Magnetic Rotary Encoder with SSI and PWM Output incl. Diagnostic Functions | AS5045-ASST | ams | ams | Navigation | Absolute position sensing with 0.09 deg resolution.
16 | 2 | $73.35 | MLX90620 FIRray:16X4 Far InfraRed Array | MLX90620 | Melexis | Future Electronics | Navigation | I2C interface. ~23 ft range.

1 1/17/2013 12:46 PM

## Autonomous Lifeguard Project

### Itemized Budget

Item # | Qty | Cost (each) | Description | Part # | Manufactu rer | Vendor | Category | Notes
17 | 4 | $20.03 | Infrared Proximity Sensor - Sharp GP2Y0A21YK | SEN-00242 | Sharp | sparkfun | Navigation | 2.6 ft.
18 | 1 | $42.89 | XBee Pro 60mW U.FL Connection - Series 1 (802.15.4) | WRL-08710 | Digi | sparkfun | Communi cation | UART interface. External antenna, 1 mi range, 250 kbps max
19 | 2 | $42.89 | XBee Pro 60mW PCB Antenna - Series 1 (802.15.4) | WRL-11216 | Digi | sparkfun | Communi cation | UART interface. PCB antenna, 1 mi range, 250 kbps max
20 | 3 | $5.18 | Breakout Board for XBee Module | BOB-08276 | | sparkfun | Communi cation | Convert to standard pin spacing.
21 | 8 | $3.08 | 2mm 10pin XBee Socket | PRT-08272 | | sparkfun | Communi cation | XBee standoffs for breakout board.
22 | 1 | $7.33 | 2.4GHz Antenna -Adhesive (U.FL connector) | WRL-11320 | TE Connectivi y | sparkfun | Communi cation | 2.4 GHz, 2 dB gain
23 | 1 | $65.12 | RFID Excalibur K9classicedp K9 Alarm | K9CLASSIC EDP | Excalibur | amazon | Communi cation | Returns rover to base waypoint. Shah tested 50 ft range.
24 | 1 | $56.30 | Super High Intensity LED Waterproof Emergency Strobe Light (BLUE/RED) | PSZLEDSTB 0421-BR | OLS | amazon | Communi cation | 12V/24V: 100mA -660mA/50mA - 330mA
25 | 2 | $5.42 | Anti-Theft High dB Lond Mini Piezo Siren for Car Alarm | B00A8DGA MQ | BestDeal USA | amazon | Communi cation | 12V DC, 150mA/90V DC, 90mA, waterproof
26 | 4 | $60.00 | Board Runs | | | | Other
27 | 1 | $150.00 | Discrete Components | | | | Other
28 | 1 | $200.00 | Materials | | | | Other | Steel, coating, acrylic, wood, MDF, foam
29 | 4 | $11.96 | PIC32MX320F128H uController | PIC32MX320 F128H | Microchip | microchipd irect | Other | 80 MHz, 16 KB RAM, 2 I2C/SPI/UART, 16 A/D, 5 timer/PWM, 2 comp., 53 I/O
30 | 3 | 38.04 | chipKIT Uno32 | CHIPKIT UNO32 | Microchip | digilentinc | Other | PIC32MX320F128 for prototyping.
31 | | $166.65 | Continuancy (5%) | | | | | Cushion for unforseen events such as additional parts and rush delivery.
Total | | 3535.42

2 1/17/2013 12:46 PM

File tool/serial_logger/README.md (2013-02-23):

# Serial Logger #

*   Website: http://lifeguardrobotics.com
*   Source: https://github.com/dagoodma/sdp/tree/master/tool/serial\_logger
*   Mailing list: [Google Groups](https://groups.google.com/a/ucsc.edu/forum/#!forum/alg-group)

This tool is used to connect to a device over serial and send and receive data while logging the interaction to a file.

## Usage ##

When run, the tool will list available serial ports and query the user to select one for connecting to. Once connected, the tool will display and record and data recieved. (TODO: Add the ability to send data.)

Follow the three steps below to use the serial logger. If you would like to use the GUI, follow step 1 from *With GUI*, and if you prefer the command line, follow step 1 from *Without GUI*. Steps 2 and 3 are the same for either method.

1. Run the tool.
    - For the GUI, on *Windows* run `serial_logger.exe`, on Mac run `serial_logger.app`.
    - Without GUI, open a terminal in `serial_logger/src`, then run `python serial_logger.py`. See _Arguments_ under the *Configuring*  section below for more information.

2. Choose serial port.
    - Windows devices are numbered ie. *COM4*
    - Mac are mounted with a serial number to the */dev* folder ie. */dev/tty.usbserial-A1012WFD*

3. Done.
    - Incoming serial data will be displayed in the console window.
    - Open *serial_logger.log* to view the recorded session.

## Configuring ##

The serial logger can be configured by setting desired parameters in *serial_logger/src/.config.cfg*. If you are using the command line, arguments may be passed which will override the config. See *Arguments* below for more details.

### Arguments ###

    python serial_logger.py -h | [-l log_file] [--loglevel=level] [-c config_file] [ -t timeout] [-b baud_rate] [device_path]

#### Positional ####
    device_path           device path or id of the serial port

#### Optional ####

    -b BAUD_RATE, --baud BAUD_RATE
                        baud rate for the serial connection (default: 9600)

    -c CONFIG_FILE, --config CONFIG_FILE
                        config file with default values (default: .config.cfg)

    -t TIMEOUT, --timeout TIMEOUT
                        serial connection timeout in seconds (default: 5)

    -l LOG_FILE, --log LOG_FILE
                        log file to record session to (default:
                        serial_logger.log)

    --loglevel {DEBUG,INFO,WARNING,ERROR,CRITICAL}
                        sets the logging level (default: INFO)

    -h, --help          show this help message and exit

## Compatibility ##

This module was written for Python 2.7.3, and has been tested on Windows 7 (64 and 32 bit), and Mac OS X ??.

TODO: Add python 3.3 support.

## Author ##

&copy; 2012-2013 David Goodman

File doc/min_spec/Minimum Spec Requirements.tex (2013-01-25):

\documentclass[11pt]{amsart}
\usepackage{geometry, color, mathtools, amsfonts, graphics,amsmath}                % See geometry.pdf to learn the layout options. There are lots.
\geometry{letterpaper}                   % ... or a4paper or a5paper or ... 
%\geometry{landscape}                % Activate for for rotated page geometry
\usepackage[parfill]{parskip}    % Activate to begin paragraphs with an empty line rather than an indent
\usepackage{graphicx}
\usepackage{amssymb}
\usepackage{epstopdf}
\DeclareGraphicsRule{.tif}{png}{.png}{`convert #1 `dirname #1`/`basename #1 .tif`.png}
\begin{document}

\title{Minimum Specification Requirements}

\author{Autonomous Lifeguard Group}
%\date{}                                           % Activate to display a given date or no date

\maketitle
{
In order to achieve a passing mark in the CMPE 129 Senior Design Series, a minimum specification must be met.
The Autonomous Lifeguard Group will be expected to demo the entire system in a body of water within a set scope of functionality. 

The demo will take place on a lake in Santa Cruz, where a waypoint will be selected by an advisor within the range of no more than 100 meters from the shoreline. A teammate will operate the Command Center obtaining GPS coordinates of the waypoint of interest. The Autonomous Surface Vessel (ASV) will be docked in the lake at a point no more than 300 meters away from the point of interest. It will be required to navigate to the waypoint within the amount of time it would take a lifeguard to swim to that point. This will be calculated with the formula below:

\section{Command Center}
The Command Center must offer ease-of-use to the operator by allowing for swift maneuverability and a push-button interface for commands and operation. It is to be mounted at a location on the shore at least 15 feet above water level. The Command Center must be able to obtain the latitudinal and longitudinal coordinates of the selected waypoint, and wirelessly communicate the coordinates to the ASV at a distance of at least 350 meters.

\section{Autonomous Surface Vessel}
The Autonomous Surface Vessel must be deployable from a location in the water within the above mentioned waypoint radius (300m from waypoint). In addition, the ASV must have enough buoyancy to support a person. The ASV must be able to wirelessly communicate with the Command Center at a distance of at least 350 meters. Finally, the ASV must be able to reach its target waypoint within the amount of time it would take a lifeguard to swim there.

}

\end{document}

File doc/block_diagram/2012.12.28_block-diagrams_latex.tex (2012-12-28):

\documentclass{article}
\usepackage[pdftex]{graphicx}
\usepackage{epstopdf}
\usepackage{amsmath, amssymb, calc}
\usepackage{mathtools}
\usepackage{siunitx}
\usepackage{verbatim}
\usepackage{caption}
\usepackage{float}
\usepackage{multirow}
\usepackage{caption}
\usepackage{subcaption}
\usepackage{enumerate}
\usepackage{steinmetz}
\usepackage{lastpage}
\usepackage{fancyhdr}

\pagestyle{fancy}
\lhead{Darrel Deo, Shehadah Dajani,\\ John Ash, David Goodman}
\rhead{Autonomous Lifeguard,\\ Fall 2012}
\chead{\thepage\ of \pageref{LastPage}}
\lfoot{Autonomous Lifeguard --- Block Diagram}
\cfoot{}
\renewcommand{\headrulewidth}{0.4pt}
\renewcommand{\footrulewidth}{0.4pt}

\newcommand*\sepline{%
  \begin{center}
    \rule[1ex]{.5\textwidth}{.5pt}
  \end{center}}

\usepackage{blindtext}
\begin{document} 

\begin{center}
{\bf \Large Autonomous Lifeguard\\
	Block Diagrams}
\end{center}

\begin{figure}[H]
		\begin{center}
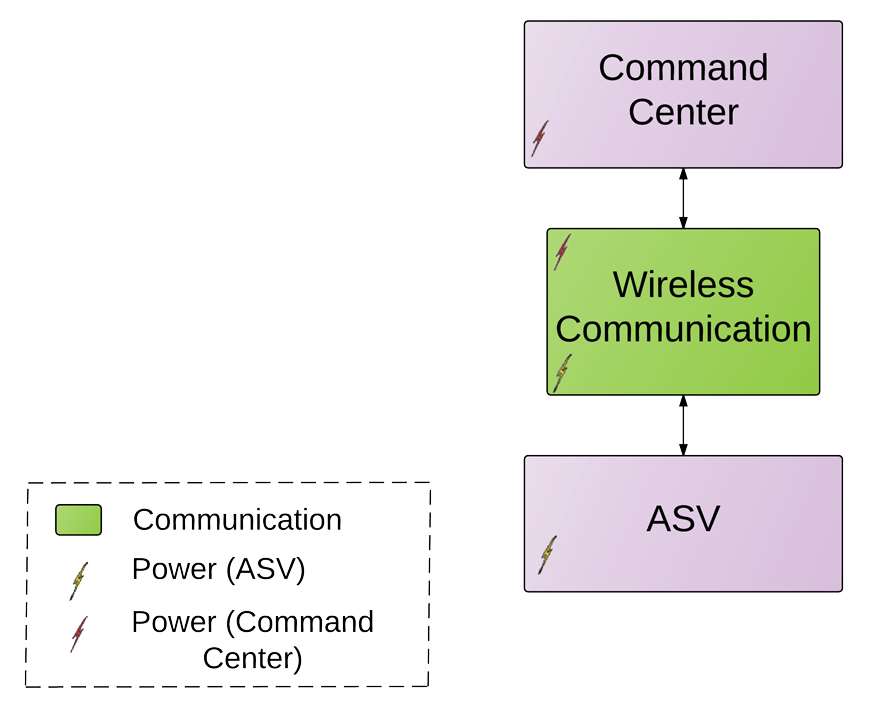
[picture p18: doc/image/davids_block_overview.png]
		\centerline{}
		\caption{System Overview}
		%\label{fig:1_freqz}
		\end{center}
	\end{figure}

\begin{figure}[H]
	\centering
\begin{subfigure}[b]{1\linewidth}		
	\begin{center}
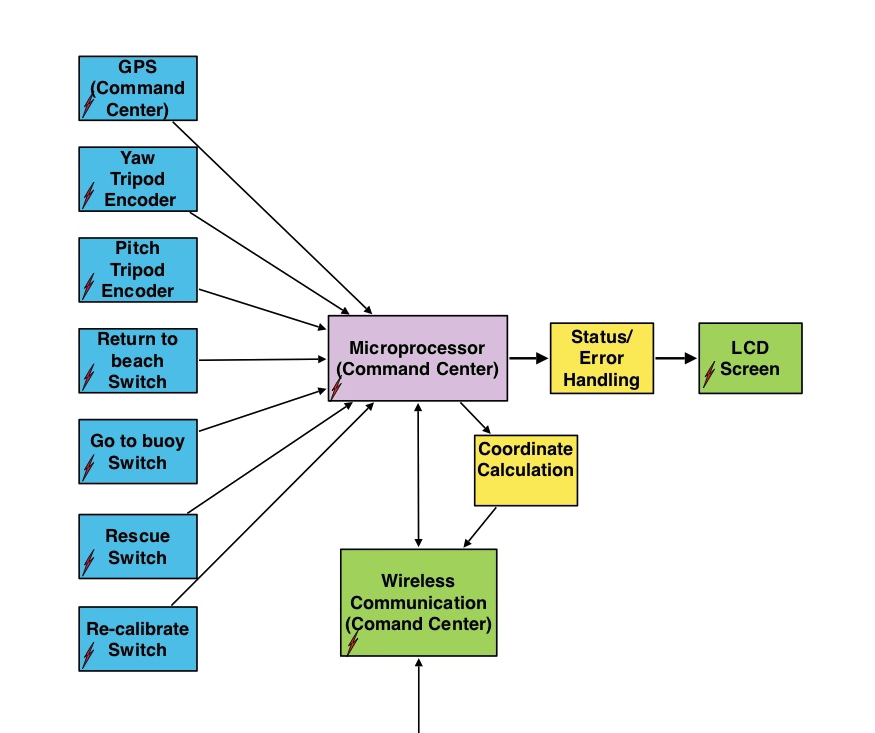
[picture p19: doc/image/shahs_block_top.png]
	\centerline{}
	%\caption{Schematic}
	%\label{fig:rgb_schem}
	\end{center}
\end{subfigure}
\begin{subfigure}[bH]{1\linewidth}
	\begin{center}
	\centerline{}
	%\caption{Specifications}
	%\label{fig:rgb_spec}
	\end{center}
	\end{subfigure}%
	\caption{Command Center Block Diagram}
	%\label{fig:connect4}
\end{figure}

\begin{figure}[H]
	\centering
\begin{subfigure}[b]{1\linewidth}		
	\begin{center}
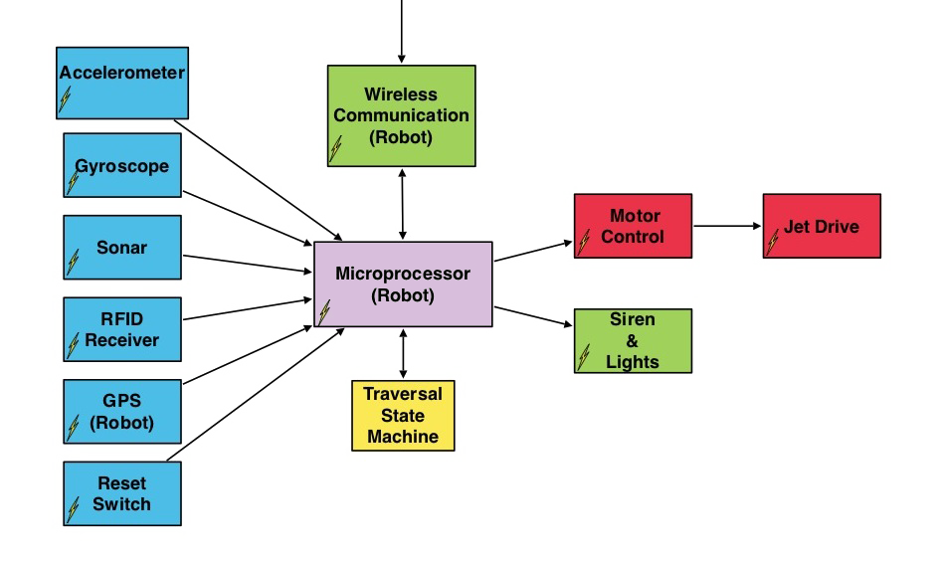
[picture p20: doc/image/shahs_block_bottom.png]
	\centerline{}
	%\caption{Schematic}
	%\label{fig:rgb_schem}
	\end{center}
\end{subfigure}
\begin{subfigure}[bH]{1\linewidth}
	\begin{center}
	\centerline{}
	%\caption{Specifications}
	%\label{fig:rgb_spec}
	\end{center}
	\end{subfigure}%
	\caption{ASV Block Diagram}
	%\label{fig:connect4}
\end{figure}

\end{document}

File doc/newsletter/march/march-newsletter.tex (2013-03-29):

%%% LaTeX Template: Newsletter
%%%
%%% Source: http://www.howtotex.com/
%%% Feel free to distribute this template, but please keep the referal to HowToTeX.com.
%%% Date: September 2011

%%% ---------------
%%% PREAMBLE
%%% ---------------
\documentclass[10pt,a4paper]{article}

% Define geometry (without using the geometry package)
\setlength\topmargin{-48pt}
\setlength\headheight{0pt}
\setlength\headsep{25pt}
\setlength\marginparwidth{-20pt}
\setlength\textwidth{7.0in}
\setlength\textheight{9.5in}
\setlength\oddsidemargin{-30pt}
\setlength\evensidemargin{-30pt}

\frenchspacing						% better looking spacing

% Call packages we'll need
\usepackage[english]{babel}			% english
\usepackage{graphicx}				% images
\usepackage{amssymb,amsmath}		% math
\usepackage{multicol}				% three-column layout
\usepackage{url}					% clickable links
\usepackage{marvosym}				% symbols
\usepackage{wrapfig}				% wrapping text around figures
\usepackage[T1]{fontenc}			% font encoding
\usepackage{charter} 				% Charter font for main content
\usepackage{blindtext}				% dummy text
\usepackage{datetime}				% custom date
\usepackage{caption}
	\newdateformat{mydate}{\monthname[\THEMONTH] \THEYEAR}
\usepackage[pdfpagemode=FullScreen,
			colorlinks=false]{hyperref}	% links and pdf behaviour

% Customize (header and) footer
\usepackage{fancyhdr}
\pagestyle{fancy}
\lfoot{	\footnotesize 
		Newletter from LifeguardRobotics.com \\
		\Mundus\ \href{http://www.lifeguardrobotics.com}{LifeguardRobotics.com}	\quad
		\Telefon\ (831) 704-6771										\quad
		\Letter\ \href{mailto:lifeguardrobotics@gmail.com}{lifeguardrobotics@gmail.com}
	  }
\cfoot{}
\rfoot{\footnotesize ~\\ Page \thepage}
\renewcommand{\headrulewidth}{0.0pt}	% no bar on top of page
\renewcommand{\footrulewidth}{0.4pt}	% bar on bottom of page

%%% ---------------
%%% DEFINITIONS
%%% ---------------

% Define separators
\newcommand{\HorRule}[1]{\noindent\rule{\linewidth}{#1}} % Creating a horizontal rule
\newcommand{\SepRule}{\noindent							 % Creating a separator
						\begin{center}
							\rule{250pt}{1pt}
						\end{center}
						}						

% Define Title en News input
\newcommand{\JournalName}[1]{%
		\begin{center}	
			\Huge \usefont{T1}{cmr}{m}{n}
			#1%
		\end{center}	
		\par \normalsize \normalfont}
		
\newcommand{\JournalIssue}[1]{%
        \hfill \textsc{\mydate \today, No #1}
        \par \normalsize \normalfont}

\newcommand{\NewsItem}[1]{%
		\usefont{T1}{augie}{m}{n} 	
		\large #1 \vspace{4pt}
		\par \normalsize \normalfont}
		
\newcommand{\NewsAuthor}[1]{%
			\hfill by \textsc{#1} \vspace{4pt}
			\par \normalfont}		

%%% ---------------
%%% BEGIN DOCUMENT
%%% ---------------
\begin{document}
% Title	
% -----
\JournalIssue{2}
\JournalName{The Autonomous Lifeguard Project}
\noindent\HorRule{3pt} \\[-0.75\baselineskip]
\HorRule{1pt}
% -----

% Front article
% -----
\vspace{0.5cm}
	\SepRule
\vspace{0.5cm}
\begin{center}
\begin{minipage}[h]{0.80\linewidth}
	\begin{wrapfigure}{l}{0.378\textwidth}
		{%
		\setlength{\fboxsep}{0pt}%
		\setlength{\fboxrule}{1pt}%
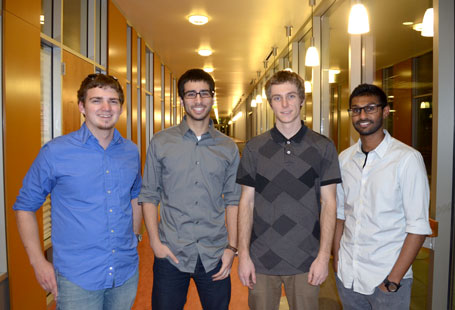
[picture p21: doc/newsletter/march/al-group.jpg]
		\fbox{}%
		\caption*{Left to right: J. Ash, S. Dajani, D. Goodman, D. Deo}
		}%
		%\\	% this spacer is needed to make the text on the right fit OK
	\end{wrapfigure}
	
	\NewsItem{Who Are We}
	\emph{We are a group of UC Santa Cruz computer and robotics engineering students who are building a robot to assist lifeguards in saving drowning individuals on beaches, at sea, and in other bodies of water. In the United States, there has been a reported 99 people that have drowned in the past year alone, with a good number of them occurring while a lifeguard was on duty. We propose an autonomous boat that can navigate to a person, allowing them to hang on and stay a float until the lifeguard arrives. Our aim is to keep beaches safer by reducing the risk of drowning.}
\end{minipage}
\end{center}
% -----

% 
% -----
\vspace{0.5cm}
	\SepRule
\vspace{0.5cm}
\begin{multicols}{3}
	\NewsItem{Milestones}
	\NewsAuthor{D. Goodman}
    
    We are all very pleased to announce that our command center is nearing completion. As March comes to an end, our project continues to grow and progress. Throughout this month, many hours were dedicated to implementing and integrating sensors, performing testing, and debugging the command center. Last week, we met our desired basic functionality for the command center, and created a video demonstrating its usage. A technical presentation was given before an audience of our peers that discussed our progress, challenges, and future plans.
\begin{center}
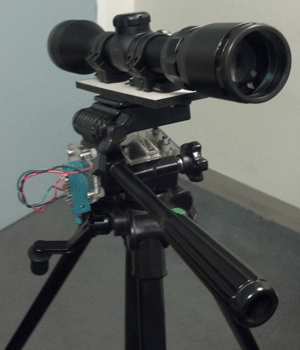
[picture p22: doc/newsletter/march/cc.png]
			
		\end{center}
The months of February and March have brought our team closer to reaching our goals. The completion of our boat is the next major milestone. We plan to accomplish this during April and May, so that by June we will have a working prototype. 
		
% -----

\vspace{1cm}
% Other news (2)
% -----
\NewsItem{Future Work}
\NewsAuthor{D. Goodman}
	Although the engineering buildings are very quiet during spring break, we are currently working hard to get the boat into the water. Shehadeh is working diligently to equip the boat with the new motors and emergency RC receiver. These modifications will allow us to reach a drowning victim quickly, and safely. Darrel, David, and John are busy implementing autonomous features into the boat, via a navigation and drive system. Our goal is to have the boat navigating on its own in the water by this coming weekend.

Following this weekend's testing, we will continue to work on the navigation system, and to get the command center talking to the boat from the shore. Once the boat is able to navigate to waypoints, we will begin the integration of our human detection sensor array, which includes sonar and thermal imaging. We are eager to continue making progress in every direction, and spring is proving to be very productive so far.

% -----
%\columnbreak
\vspace{1cm}
% Other news (2)
% -----
\NewsItem{Support}
\NewsAuthor{D. Deo}
The Autonomous Lifeguard Group would like to extend their utmost appreciation to those who have supported our cause. With the help of our donors, we have been able to partially fund our ambitious project. Done with the ComPAS, we will now focus our efforts on the AtLAs in hopes to complete our project within the coming months. We do ask that anyone interested in contributing to our project visit our team website and donate. All forms of support are welcome.
\end{multicols}
% -----
\end{document}

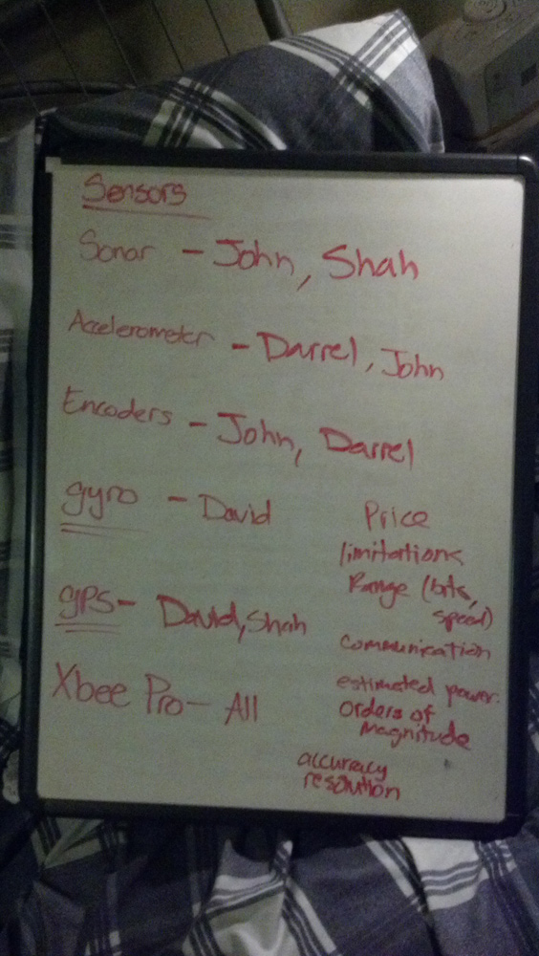
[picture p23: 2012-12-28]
doc/image/2012.09.20_sensor_assignments.jpg

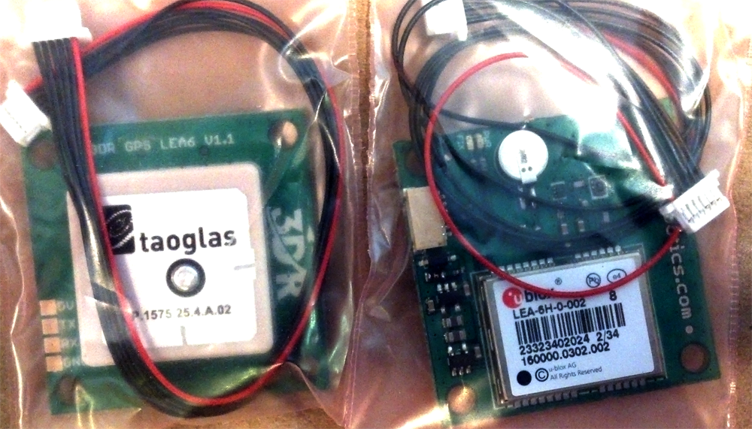
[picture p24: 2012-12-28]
doc/image/ublox_gpses.png

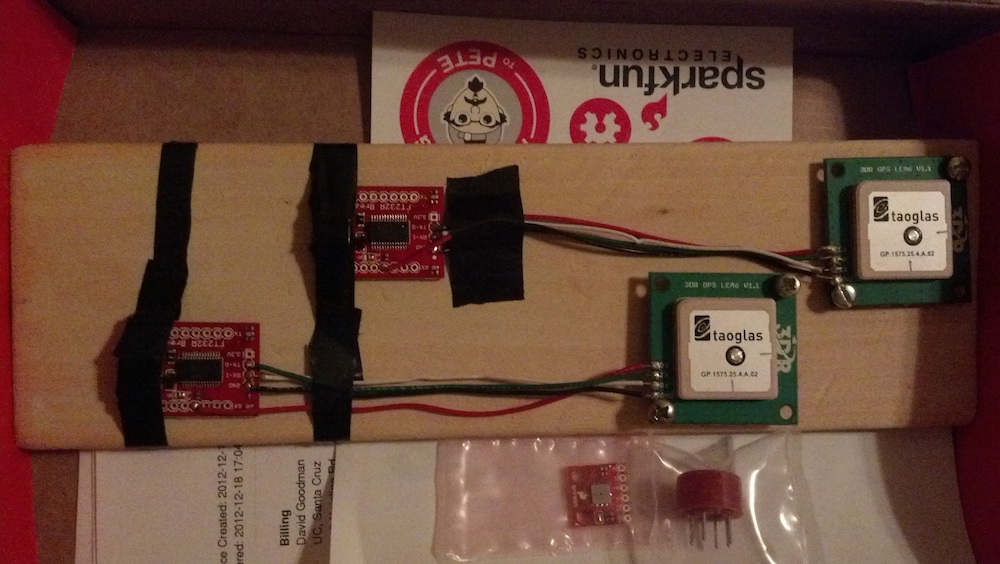
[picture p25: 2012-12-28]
doc/image/gps_proto_and_altimeter.jpg

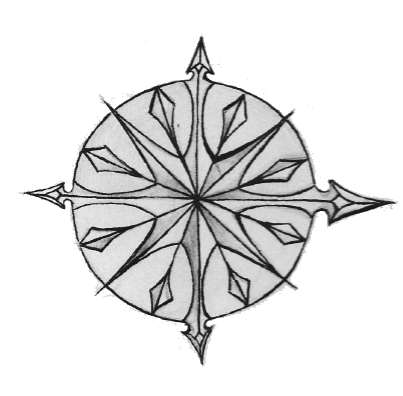
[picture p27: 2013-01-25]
doc/doxygen/api/html/compas.png

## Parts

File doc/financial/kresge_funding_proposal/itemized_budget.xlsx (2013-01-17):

Item # | Qty | Cost (each) | Description | Part # | Manufacturer | Vendor | Category | Notes | Link | Purchaser
1 | 2 | $173.63 | 45" RC Boat Hull (Giant Racer G-75 Mosquito Craft) | B757T6030 | STOP | amazon | Aquatic | Going to test, then possibly modify or return. | http://www.amazon.com/Mosquito-Racing-Electric-Control-Cooling/dp/B002F9TTBK | Shah
2 | 4 | $30.00 | RC Boat Fender Skirt (Polyform G-4 Twin Eye Fender 6.5 x 23 - Black w/Air Adapter) | G-4-BLACK | Polyform | Boater's Marine Supply | Aquatic |  | http://www.boatersmarinesupply.com/m7/36797--polyform-g-4-twin-eye-fender-6-5-x-23-black-w-air-adapter.html
3 | 1 | $105.00 | Polyurethane Expanding Foam (2 gal kit 50/50 mix) |  | Various | Boat Builder Central | Aquatic | 480 lbs of buoyancy U.S. Coast Guard Approved | http://boatbuildercentral.com/proddetail.php?prod=E_foam_2gal#.UKcDTpgR4nw
4 | 3 | $53.09 | AquaCraft 28-35-2200kV Brushless Motor MiniMono | AQUB1805 | AquaCraft | Tower Hobbies | Aquatic |  | http://www3.towerhobbies.com/cgi-bin/wti0001p?&I=LXBHKN&P=M
5 | 3 | $28.69 | Aquacraft Grim Racer 40X52/3, 3 Blade Prop, LH | AQUB9720 | AquaCraft | funrcboats | Aquatic | 40mm (1.57") x 52MM Pitch. Copper-Beryllium-Titanium. Must hand finish. | http://www.funrcboats.com/ProductInfo.aspx?productid=AQUB9720
6 | 2 | $53.09 | AquaCraft 20-Amp LiPo ESC Minimono | LXBHKP | AquaCraft | Tower Hobbies | Aquatic, Power | 20 Amp | http://www3.towerhobbies.com/cgi-bin/wti0001p?&I=LXBHKP&P=0
7 | 2 | $70.82 | Turnigy nano-tech 5000mah 4S 45~90C Lipo Battery Pack | N5000.4S.45 | TURNIGY | Hobby King | Power | 5000mAh, 4 Cell (14.8V), 45C Constant / 90C Burst | http://www.hobbyking.com/hobbyking/store/__11957__turnigy_nano_tech_5000mah_4s_45_90c_lipo_pack.html
8 | 2 | $128.83 | Waterproof NEMA 4X enclosure | HW-J161406SC | Nema | automationdirect | Aquatic | 4SCREWS OPQ CVR GRY 4X 16X14X6IN | http://www.automationdirect.com/adc/Shopping/Catalog/Enclosures/Non-Metal_(NEMA_4X_-a-_3R)/JIC_(6_in._X_4_in._to_20_in._X_16_in.)/HW-J161406SC
9 | 2 | $91.88 | 3DR GPS uBlox LEA-6 Breakout | LEA-6H | uBlox | 3drobotics | Navigation | UART, USB interfaces. Includes ceramic antenna, LNA, SAW filter, and 3.3V batt. | http://store.diydrones.com/3DR_GPS_LEA_6_p/br-3drlea-6.htm | David
10 | 2 | $31.50 | Barometric Pressure Sensor - BMP085 Breakout | SEN-11282 | Bosch | sparkfun | Navigation | I2C interface. Piezoelectric, includes temp. sensor. | https://www.sparkfun.com/products/9694 | David
11 | 1 | $18.04 | Triple Axis Accelerometer Breakout | MMA8452Q | Freescale Semi | sparkfun | Navigation | I2C interface. 3-axis, 2 ISR pins, optional HPF. | https://www.sparkfun.com/products/10955 | David
12 | 1 | $61.18 | Triple-Axis Digital-Output Gyro ITG-3200 Breakout | ITG-3200 | InvenSense | sparkfun | Navigation | I2C interface. 3-axis, optional LPF, and ISR pin. | https://www.sparkfun.com/products/9801
13 | 1 | $246.26 | Barska Blackhawk ED Spotting Scope 20-60x 60mm Angled Body | AD11520 | Barska | midwayusa | Navigation | Great at 600-800ft. 60mm, 20-60x. | http://www.midwayusa.com/product/766437/barska-blackhawk-ed-spotting-scope-20-60x-60mm-angled-body-with-tripod-and-hard-case-rubber-armored-black
14 | 1 | $96.19 | Vortex High Country Backpack Tripod | HCOUNTRY | Vortex | midwayusa | Navigation | Full size, 4.48 ft tall, 2.1 lbs. | http://www.midwayusa.com/product/623795/vortex-high-country-backpack-tripod
15 | 4 | $22.51 | 12-bit Absolute Magnetic Rotary Encoder with SSI and PWM Output incl. Diagnostic Functions | AS5045-ASST | ams | ams | Navigation | Absolute position sensing with 0.09 deg resolution. | http://www.ams.com/eng/Products/Magnetic-Position-Sensors/Magnetic-Rotary-Position-Sensors/AS5045/(oi)/1 | David sampled
16 | 2 | $73.35 | MLX90620 FIRray:16X4 Far InfraRed Array | MLX90620 | Melexis | Future Electronics | Navigation | I2C interface. ~23 ft range. | http://www.futureelectronics.com/en/Technologies/Product.aspx?ProductID=MLX90620ESFBAD000TUMELEXIS7020660&IM=0
17 | 4 | $20.03 | Infrared Proximity Sensor - Sharp GP2Y0A21YK | SEN-00242 | Sharp | sparkfun | Navigation | 2.6 ft. | https://www.sparkfun.com/products/242
18 | 1 | $42.89 | XBee Pro 60mW U.FL Connection - Series 1 (802.15.4) | WRL-08710 | Digi | sparkfun | Communication | UART interface. External antenna, 1 mi range, 250 kbps max | https://www.sparkfun.com/products/8710 | John
19 | 2 | $42.89 | XBee Pro 60mW PCB Antenna - Series 1 (802.15.4) | WRL-11216 | Digi | sparkfun | Communication | UART interface. PCB antenna, 1 mi range, 250 kbps max | https://www.sparkfun.com/products/11216 | John
20 | 3 | $5.18 | Breakout Board for XBee Module | BOB-08276 |  | sparkfun | Communication | Convert to standard pin spacing. | https://www.sparkfun.com/products/8276? | John
21 | 8 | $3.08 | 2mm 10pin XBee Socket | PRT-08272 |  | sparkfun | Communication | XBee standoffs for breakout board. | https://www.sparkfun.com/products/8272 | John
22 | 1 | $7.33 | 2.4GHz Antenna - Adhesive (U.FL connector) | WRL-11320 | TE Connectiviy | sparkfun | Communication | 2.4 GHz, 2 dB gain | https://www.sparkfun.com/products/11320 | John
23 | 1 | $65.12 | RFID Excalibur K9classicedp K9 Alarm | K9CLASSICEDP | Excalibur | amazon | Communication | Returns rover to base waypoint. Shah tested 50 ft range. | http://www.amazon.com/Excalibur-K9classicedp-Alarm-Interupt-Includ/dp/B003NGCTS4
24 | 1 | $56.30 | Super High Intensity LED Waterproof Emergency Strobe Light (BLUE/RED) | PSZLEDSTB0421-BR | OLS | amazon | Communication | 12V/24V: 100mA - 660mA/50mA - 330mA | http://www.amazon.com/gp/product/B009EFJBHK/ref=noref?ie=UTF8&psc=1&s=automotive
25 | 2 | $5.42 | Anti-Theft High dB Lond Mini Piezo Siren for Car Alarm | B00A8DGAMQ | BestDealUSA | amazon | Communication | 12V DC, 150mA/90V DC, 90mA, waterproof | http://www.amazon.com/BestDealUSA-Anti-Theft-Piezo-Siren-Alarm/dp/B00A8DGAMQ
26 | 4 | $60.00 | Board Runs |  |  |  | Other
27 | 1 | $150.00 | Discrete Components |  |  |  | Other
28 | 1 | $200.00 | Materials |  |  |  | Other | Steel, coating, acrylic, wood, MDF, foam
29 | 4 | $11.96 | PIC32MX320F128H uController | PIC32MX320F128H | Microchip | microchipdirect | Other | 80 MHz, 16 KB RAM, 2 I2C/SPI/UART, 16 A/D, 5 timer/PWM, 2 comp., 53 I/O | http://www.microchipdirect.com/ProductSearch.aspx?keywords=PIC32MX320F128H | David sampled
30 | 3 | 38.04 | chipKIT Uno32 | CHIPKIT UNO32 | Microchip | digilentinc | Other | PIC32MX320F128 for prototyping. | http://www.digilentinc.com/Products/Detail.cfm?Prod=CHIPKIT-UNO32
31 |  | $166.65 | Continuancy (5%) |  |  |  |  | Cushion for unforseen events such as additional parts and rush delivery.
Total |  | 3535.42

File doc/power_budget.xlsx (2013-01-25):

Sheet: Atlas
Item # | Device | Power Source | Power Rails (V) |  |  | Supply Current (mA) |  | Power Consumption (mW)
 |  |  | Min | Typical | Max | Min | Max | Min | Max | Notes | Datasheet Link
1 | uBlox LEA-6 GPS | NiMH-1 (5xAA) | 2.70 | 3.30 | 3.60 | 10.91 | 36.67 | 36.00 | 121.00 | 3DR board has battery and LDO | http://www.u-blox.com/images/downloads/Product_Docs/LEA-6_ProductSummary_%28GPS.G6-HW-09002%29.pdf
1a | MAXIM GPS LNA | NiMH-1 (5xAA) | 1.60 | 3.30 | 3.60 | 4.10 | 5.60 | 13.53 | 167.00 |  | http://pdfserv.maximintegrated.com/en/ds/MAX2659.pdf
2 | MMA8452 Accelerometer | NiMH-1 (5xAA) | 1.95 | 3.30 | 3.60 | 0.01 | 0.17 | 0.02 | 0.56 |  | http://dlnmh9ip6v2uc.cloudfront.net/datasheets/Sensors/Accelerometers/MMA8452Q.pdf
3 | Xbee with PCB Antenna | NiMH-1 (5xAA) | 2.80 | 3.30 | 3.40 | 55.00 | 250.00 | 181.50 | 825.00 | Xbee pro uses 6x more current than Xbee | http://www.sparkfun.com/datasheets/Wireless/Zigbee/XBee-Datasheet.pdf
3a | Xbee with RPSMA Antenna | NiMH-1 (5xAA) | 2.80 | 3.30 | 3.40 | 55.00 | 340.00 | 181.50 | 1122.00 |  | http://www.sparkfun.com/datasheets/Wireless/Zigbee/XBee-Datasheet.pdf
4 | Sonar @ 3.3V | NiMH-1 (5xAA) | 3.00 | 3.30 | 5.50 | 2.10 | 50.00 | 6.93 | 165.00 |  | http://www.maxbotix.com/documents/MB7066-MB7076_Datasheet.pdf
4a | Sonar @ 5V | NiMH-1 (5xAA) | 3.00 | 5.00 | 5.50 | 3.40 | 100.00 | 17.00 | 500.00 | More distance | http://www.maxbotix.com/documents/MB7066-MB7076_Datasheet.pdf
5 | Thermal Array | NiMH-1 (5xAA) | 2.20 | 2.60 | 3.60 | 5.00 | 7.00 | 13.00 | 25.20 | the thermal array will operate at the most sensitively at 2.6V | http://www.melexis.com/Asset/Datasheet-IR-thermometer-16X4-sensor-array-MLX90620-DownloadLink-6099.aspx
6 | GH100 Microwave Motion Sensor | NiMH-1 (5xAA) | 4.75 | 5.00 | 5.25 | 30.00 | 40.00 | 150.00 | 200.00 |  | http://pub.ucpros.com/download/GH100Datasheet.pdf
9 | Barometer | NiMH-1 (5xAA) | 1.62 | 3.30 | 3.60 | 0.00 | 1.00 | 0.00 | 3.30 | 1mA during conversion, otherwise 0 | http://dlnmh9ip6v2uc.cloudfront.net/datasheets/Sensors/Pressure/BST-BMP085-DS000-06.pdf
10 | RFID Excalibur K9classicedp K9 Alarm | NiMH-1 (5xAA) | 9.00 | 12.00 | 13.00 | 0.00 | 750.00 | 0.00 | 9000.00 | Pg. 23: The source connection must have at least a 15 Amp capacity at all times | http://www.caralarm.com/manuals/k-9/k9-mundial.pdf
8 | Motors and ESC | LIPO-1 (3S) | 7.40 | 9.25 | 11.10 | 0.00 | 35000.00 | 0.00 | 388500.00 | Powered by 2S or 3S LiPo batteries. | http://www.hobbytown.com/Shop/Reaktor-3500kv-Brushless-Motor-Combo/
8 | Motors and ESC | LIPO-2 (3S) | 7.40 | 9.25 | 11.10 | 0.00 | 35000.00 | 0.00 | 388500.00
11 | Rotating Beacon Light | AA Batteries (2x) |  |  |  |  |  |  |  | Uses batteries.

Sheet: Compas
Item # | Device | Power Source | Power Rails (V) |  |  | Supply Current (mA) |  | Power Consumption (mW)
 |  |  | Min | Typical | Max | Min | Max | Min | Max | Notes | Datasheet Link
1 | uBlox LEA-6 GPS | NiMH-2 (5xAA) | 2.70 | 3.30 | 3.60 | 10.91 | 36.67 | 36.00 | 121.00 | 3DR board has battery and LDO | http://www.u-blox.com/images/downloads/Product_Docs/LEA-6_ProductSummary_%28GPS.G6-HW-09002%29.pdf
1a | MAXIM GPS LNA | NiMH-2 (5xAA) | 1.60 | 3.30 | 3.60 | 4.10 | 5.60 | 13.53 | 167.00 |  | http://pdfserv.maximintegrated.com/en/ds/MAX2659.pdf
3 | Xbee with PCB Antenna | NiMH-2 (5xAA) | 2.80 | 3.30 | 3.40 | 55.00 | 250.00 | 181.50 | 825.00 | Xbee pro uses 6x more current than Xbee | http://www.sparkfun.com/datasheets/Wireless/Zigbee/XBee-Datasheet.pdf
3a | Xbee with RPSMA Antenna | NiMH-2 (5xAA) | 2.80 | 3.30 | 3.40 | 55.00 | 340.00 | 181.50 | 1122.00 |  | http://www.sparkfun.com/datasheets/Wireless/Zigbee/XBee-Datasheet.pdf
4 | Sonar @ 3.3V | NiMH-2 (5xAA) | 3.00 | 3.30 | 5.50 | 2.10 | 50.00 | 6.93 | 165.00 |  | http://www.maxbotix.com/documents/MB7066-MB7076_Datasheet.pdf
4a | Sonar @ 5V | NiMH-2 (5xAA) | 3.00 | 5.00 | 5.50 | 3.40 | 100.00 | 17.00 | 500.00 | More distance | http://www.maxbotix.com/documents/MB7066-MB7076_Datasheet.pdf
7 | 12-bit Rotary Encoder @ 3.3V | NiMH-2 (5xAA) | 3.00 | 3.30 | 3.60 | 16.00 | 21.00 | 52.80 | 69.30 | We will run these at 5 volts, there is an internal step down. | http://www.ams.com/eng/content/download/1288/7223/496
7a | 12-bit Rotary Encoder @ 5V | NiMH-2 (5xAA) | 4.50 | 5.00 | 5.50 | 16.00 | 21.00 | 80.00 | 105.00 | We will run these at 5 volts, there is an internal step down to 3.3V. | http://www.ams.com/eng/content/download/1288/7223/496
9 | Barometer | NiMH-2 (5xAA) | 1.62 | 3.30 | 3.60 | 0.00 | 1.00 | 0.00 | 3.30 | 1mA during conversion, otherwise 0 | http://dlnmh9ip6v2uc.cloudfront.net/datasheets/Sensors/Pressure/BST-BMP085-DS000-06.pdf

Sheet: Sources
System | Power Source | Power Consumption (W) |  |  | Current Consumption (A) |  |  | Notes
 |  | Min | Avg | Peak | Min | Avg | Peak |  | Datasheets
Atlas | NiMH-1 (5xAA) | 0.41 | 5.78 | 11.14 | 0.11 | 0.69 | 1.28 | For electronics, 9.6V, 8xAA 2000mAh TENERGY, 8.5oz | http://www.tenergy.com/Tenergy-NiMh-9-6V-2000mAh-High-Capacity-Battery-Pack-w-Tamiya-Connector_2 | http://www.tenergy.com/10306
 | LIPO-1 (3S) | 0.00 | 194.25 | 388.50 | 0.00 | 17.50 | 35.00 | For motors (1 each), 11.1V (3S) 5000mAh Venom, 15.8oz, 55.5 Wh, Cont. Discharge: 20C (100A), Charge Rate: 1C (5A), Max Burst Rate: 40C (200A), Max Volts/pack: 12.6V, Max Volts/cell: 4.2V, Min Discharge Volts/pack: 9.0V | http://www.venom-group.com/20C-3S-5000mah-11-1v-LiPO-UNI.html
 | LIPO-2 (3S) | 0.00 | 194.25 | 388.50 | 0.00 | 17.50 | 35.00 | (see LIPO-1 above)
 | AA Batteries (2x) |  |  |  |  |  |  | For siren
Compas | NiMH-2 (5xAA) | 0.51 | 1.68 | 2.84 | 0.14 | 0.45 | 0.75 | (see NiMH-1 above)

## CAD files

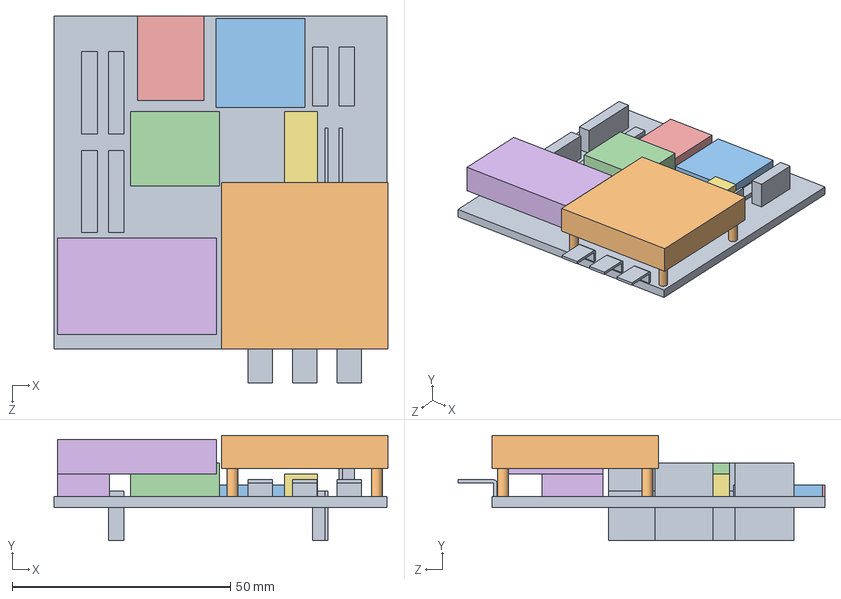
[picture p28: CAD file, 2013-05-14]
model/solidworks/AtLAs/IO Board/IO Shield.SLDASM
76.5 x 24.1 x 83.9 mm
IO Board
GPS
Compass
Override
SD Logger
Receiver
Fuse Holder

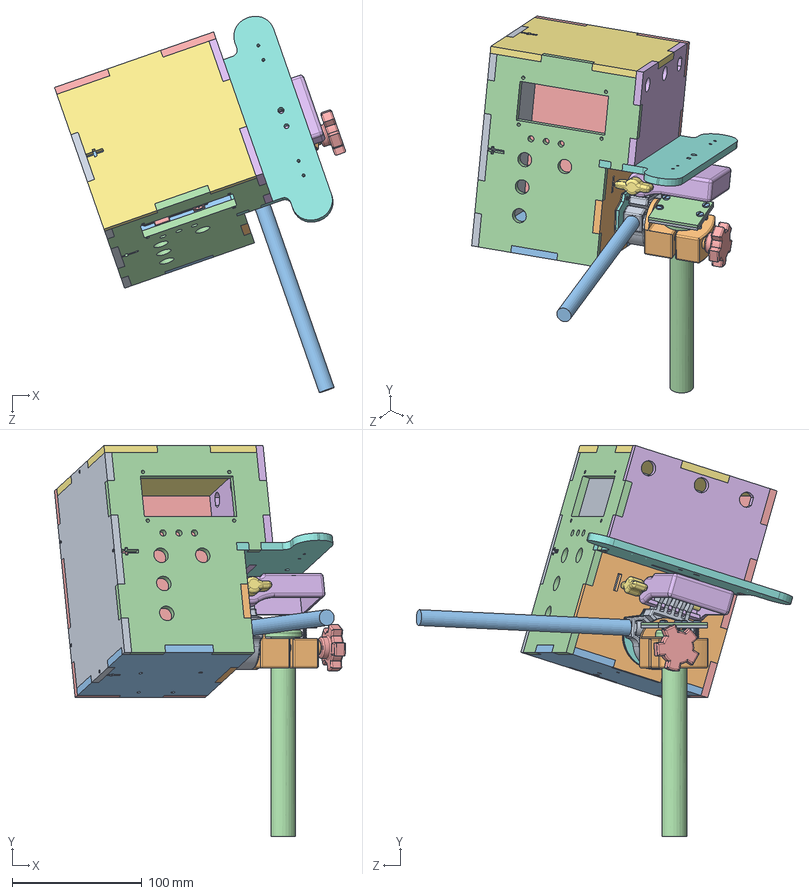
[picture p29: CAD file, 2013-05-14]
model/solidworks/Command Center/Tripod.SLDASM
224.3 x 301.3 x 290.1 mm
Pitch Platform
Pitch Disk
Pitch Arm
Yaw Wheel
Yaw Screw
Roll Base
Roll Screw
Pitch Mounts
Yaw Mount with hole
Pitch Mount no hole
binding head screw_ai x 8
Yaw Mount
Long Side
Short Side
Top
Bottom
Short Side 2
Inside L
Low Bottom
Long Side 2
Arduino UNO

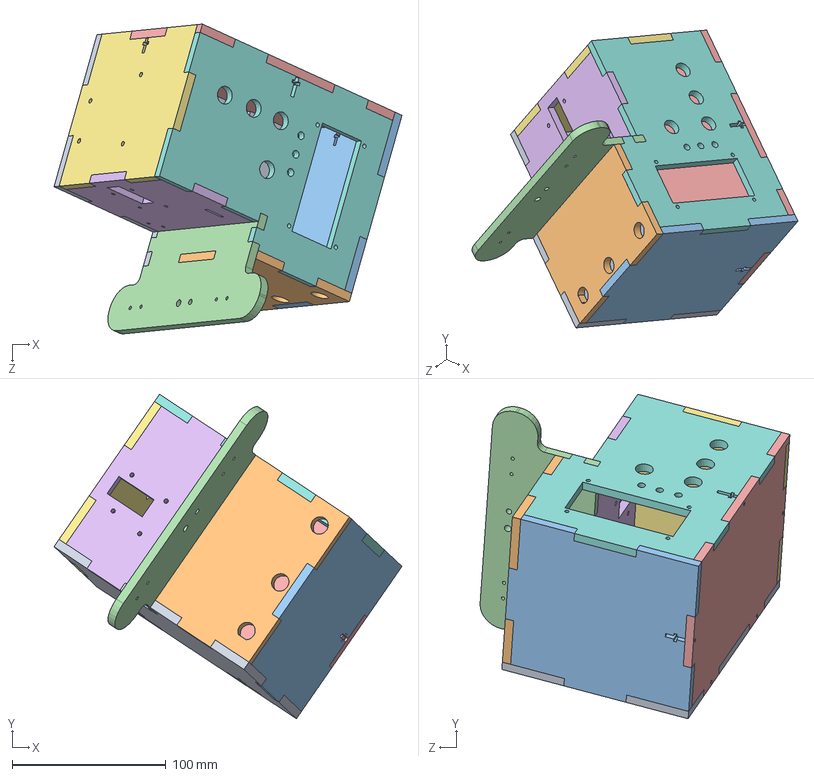
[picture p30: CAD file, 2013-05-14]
model/solidworks/Command Center/CC Box/Box.SLDASM
226.4 x 211.1 x 201.6 mm
Long Side
Short Side
Top
Bottom
Short Side 2
Inside L
Low Bottom
Long Side 2

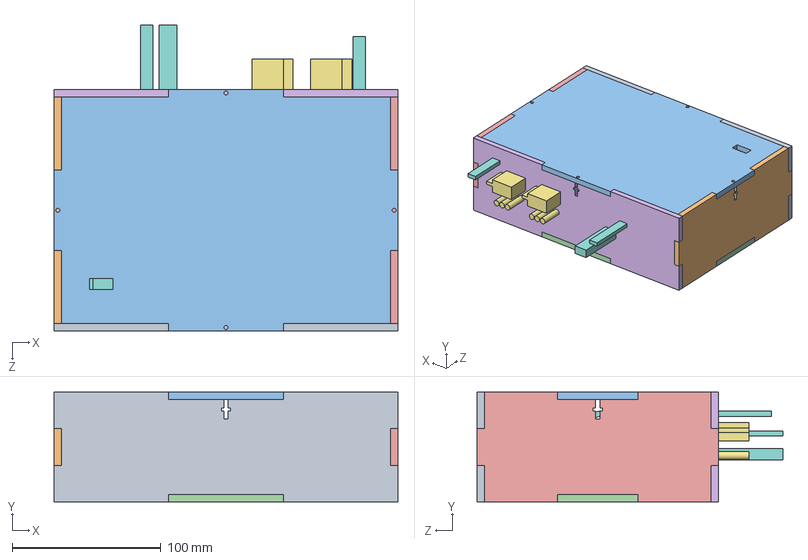
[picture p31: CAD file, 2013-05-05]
model/solidworks/AtLAs/Water Proof Box/Box.SLDASM
231.1 x 73.7 x 205.9 mm
Long Side
Short Side
Top
Bottom
Short Side Two
Long Side Two
ESC x 2
Board

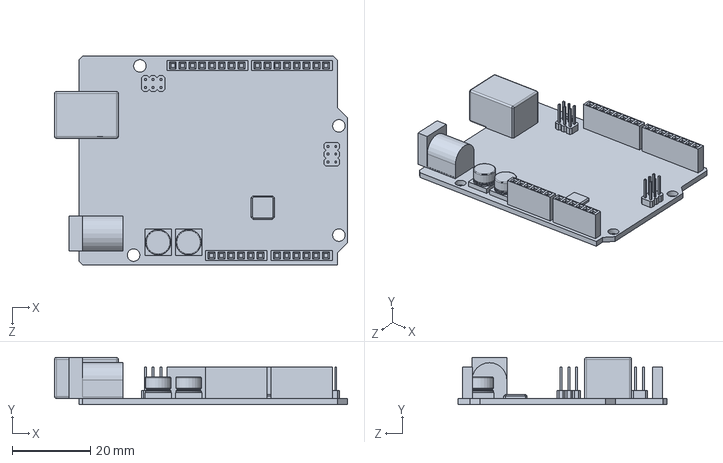
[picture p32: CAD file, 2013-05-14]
model/solidworks/Arduino UNO.SLDPRT
74.8 x 12.1 x 53.3 mm

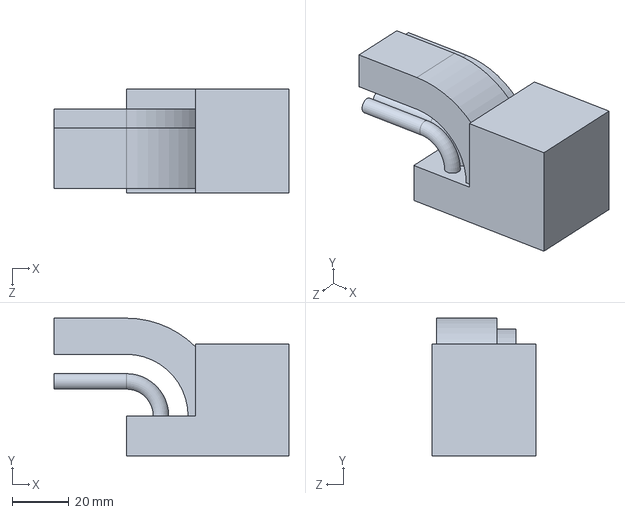
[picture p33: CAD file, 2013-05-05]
model/solidworks/AtLAs/ESC.SLDPRT
82.6 x 48.4 x 36.6 mm

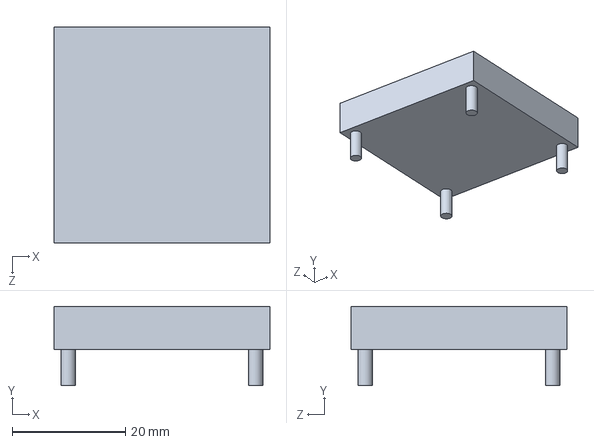
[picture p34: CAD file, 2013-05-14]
model/solidworks/AtLAs/IO Board/GPS.SLDPRT
38.1 x 14.0 x 38.1 mm

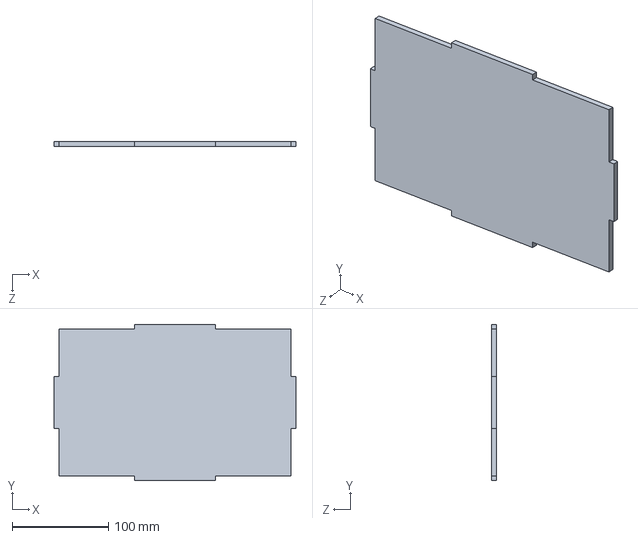
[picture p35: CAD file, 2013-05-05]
model/solidworks/AtLAs/Water Proof Box/Bottom.SLDPRT
251.5 x 162.6 x 5.08 mm

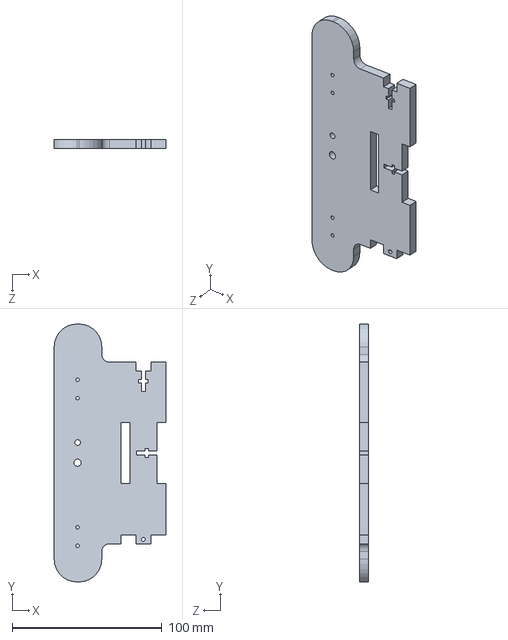
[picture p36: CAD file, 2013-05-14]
model/solidworks/Command Center/CC Box/Bottom.SLDPRT
74.5 x 172.0 x 5.99 mm

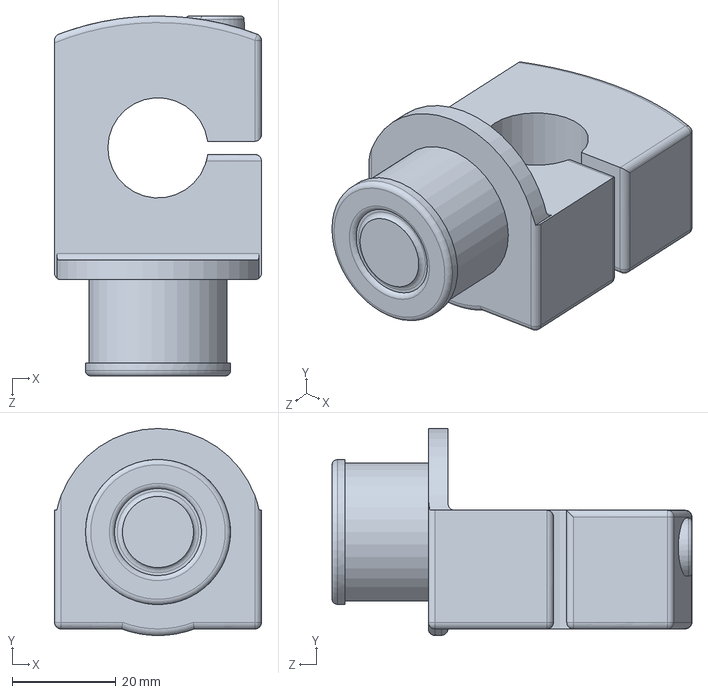
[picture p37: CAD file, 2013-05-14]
model/solidworks/Command Center/Pitch Disk.SLDPRT
39.9 x 39.9 x 69.3 mm

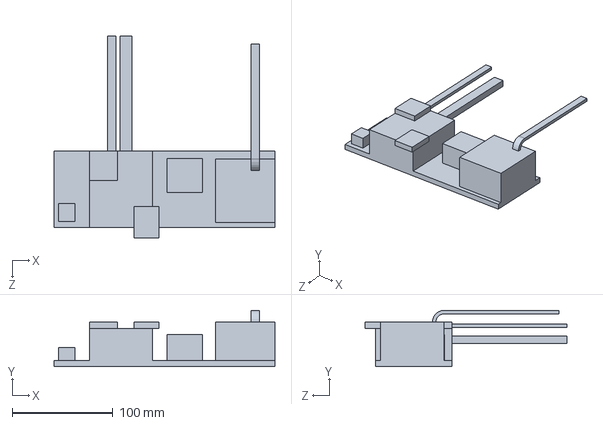
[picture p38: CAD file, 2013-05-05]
model/solidworks/AtLAs/Board.SLDPRT
219.7 x 56.0 x 200.8 mm

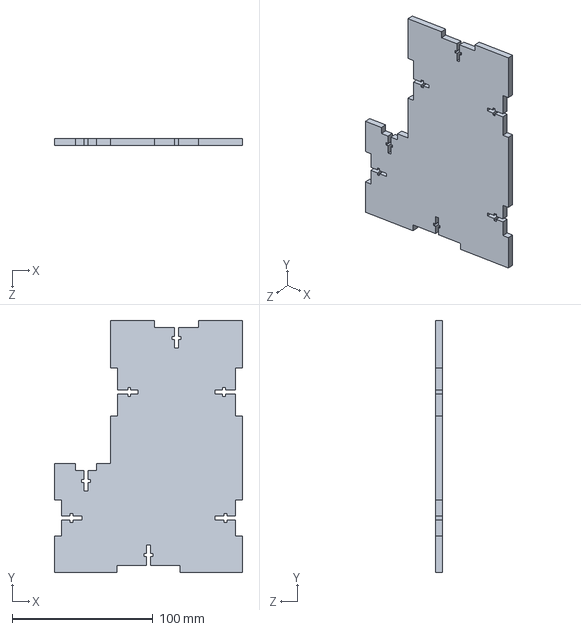
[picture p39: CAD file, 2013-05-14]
model/solidworks/Command Center/CC Box/Long Side.SLDPRT
133.9 x 179.1 x 5.08 mm

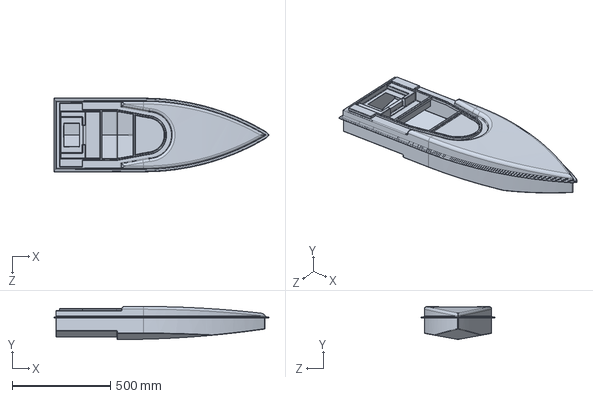
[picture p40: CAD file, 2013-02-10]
model/solidworks/AtLAs/AtLAs.SLDPRT
1092.2 x 167.8 x 374.6 mm

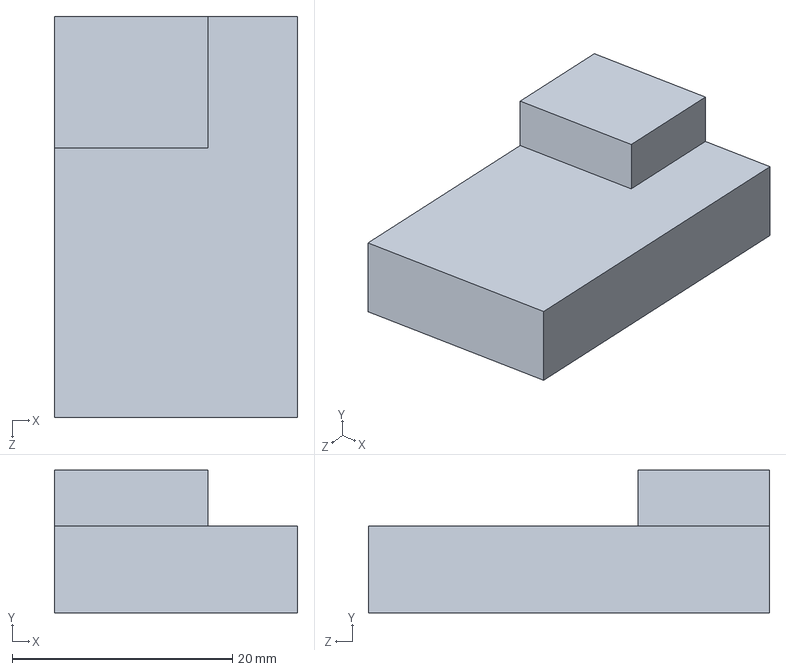
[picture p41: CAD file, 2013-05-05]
model/solidworks/AtLAs/IO Board/Receiver.SLDPRT
22.1 x 13.0 x 36.4 mm

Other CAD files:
model/solidworks/AtLAs/Water Proof Box/Short Side.SLDPRT
model/solidworks/Command Center/Yaw Mount.sldprt
model/solidworks/AtLAs/IO Board/Compass.SLDPRT
model/solidworks/Command Center/CC Box/Short Side.SLDPRT
model/solidworks/AtLAs/IO Board/Fuse Holder.SLDPRT
model/solidworks/AtLAs/IO Board/IO Board.SLDPRT
model/solidworks/AtLAs/IO Board/Override.SLDPRT
model/solidworks/AtLAs/IO Board/SD Logger.SLDPRT
model/solidworks/AtLAs/Long Side Two.SLDDRW
model/solidworks/AtLAs/Water Proof Box/BoxV1.1.DXF
model/solidworks/AtLAs/Water Proof Box/BoxV1.1.SLDDRW
model/solidworks/AtLAs/Water Proof Box/BoxV1.2.dwg
model/solidworks/AtLAs/Water Proof Box/BoxV1.2.dxf
model/solidworks/AtLAs/Water Proof Box/Long Side Two.SLDPRT
model/solidworks/AtLAs/Water Proof Box/Long Side.SLDPRT
model/solidworks/AtLAs/Water Proof Box/Short Side Two.SLDPRT
model/solidworks/AtLAs/Water Proof Box/Top.SLDPRT
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

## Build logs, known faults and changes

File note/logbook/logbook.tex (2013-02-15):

\documentclass[11pt]{article}
\usepackage[pdftex]{graphicx}
\usepackage{siunitx}
\usepackage{verbatim}
\usepackage{float}
\usepackage{lastpage}
\usepackage{fancyhdr}
\usepackage[normalem]{ulem}
\usepackage[margin=1in, paperwidth=8.5in, paperheight=11in]{geometry}
%\usepackage{indentfirst}

% Header and Footer
\pagestyle{fancy}
%\fancyhead{} % clear all header fields
%\rhead{\vspace*{1em}\headone{David Goodman}\\
%	$118$ Hainline Road $\bullet$ Aptos, CA 95003\\
%	Phone: 714.363.1280\\
%	E-Mail: dagoodma@gmail.com}
%\cfoot{}

\renewcommand{\headrulewidth}{0pt}
%\renewcommand{\footrulewidth}{0.4pt}
%\cfoot{}
%\rfoot{Goodman \thepage},

\begin{document}
\begin{center} 
{
    {\Large \textbf{Log Book Instructions}}\\
  	{\large Autonomous Lifeguard Project}
}
\end{center}

This book is to be used for recording notes and data from field tests, displaying wiring diagrams and instructions for setting up a test harness, and bug reports for both the AtLAs (water surface vehicle) and the ComPAS (command center).\\

\noindent All entries should display a title at the top left of the first page and should be signed and dated in the respective boxes at the bottom of each page. If entries span multiple pages, the next page number should be written on the bottom right, and the previous page number on the top left. If you are performing a test, be sure to write the time when you are making a note. For example:

\begin{quote}
\begin{itemize}
\item[\uline{4:31}:]{Started testing of cliff edge near light house (36.95128, -122.02692).}
\item[\uline{4:35}:]{Dropped GPS connection, but restored. Very humid conditions, tide is coming within 10 feet of the closest rock wall on the beach.}
\end{itemize}
\end{quote}

\noindent For an example of how to document the setup of a test harness see \uline{GPS Test Harness Setup} on page \ \ \ .
\end{document}

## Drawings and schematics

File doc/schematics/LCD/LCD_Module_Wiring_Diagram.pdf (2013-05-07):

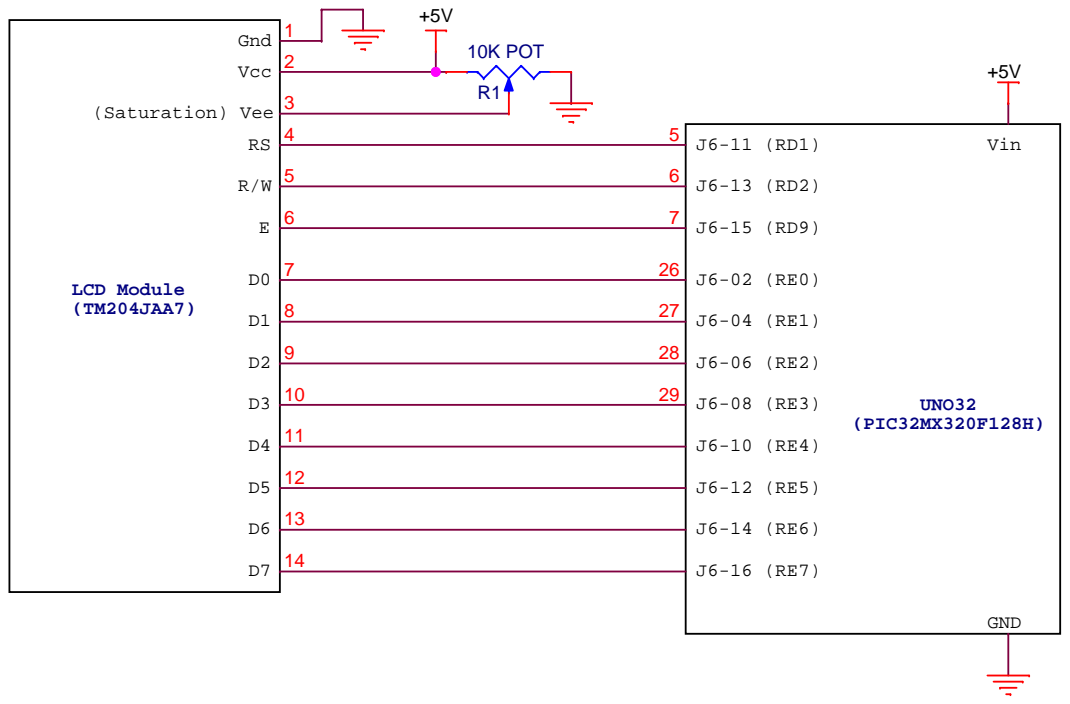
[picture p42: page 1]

LCD Module Wiring Diagram

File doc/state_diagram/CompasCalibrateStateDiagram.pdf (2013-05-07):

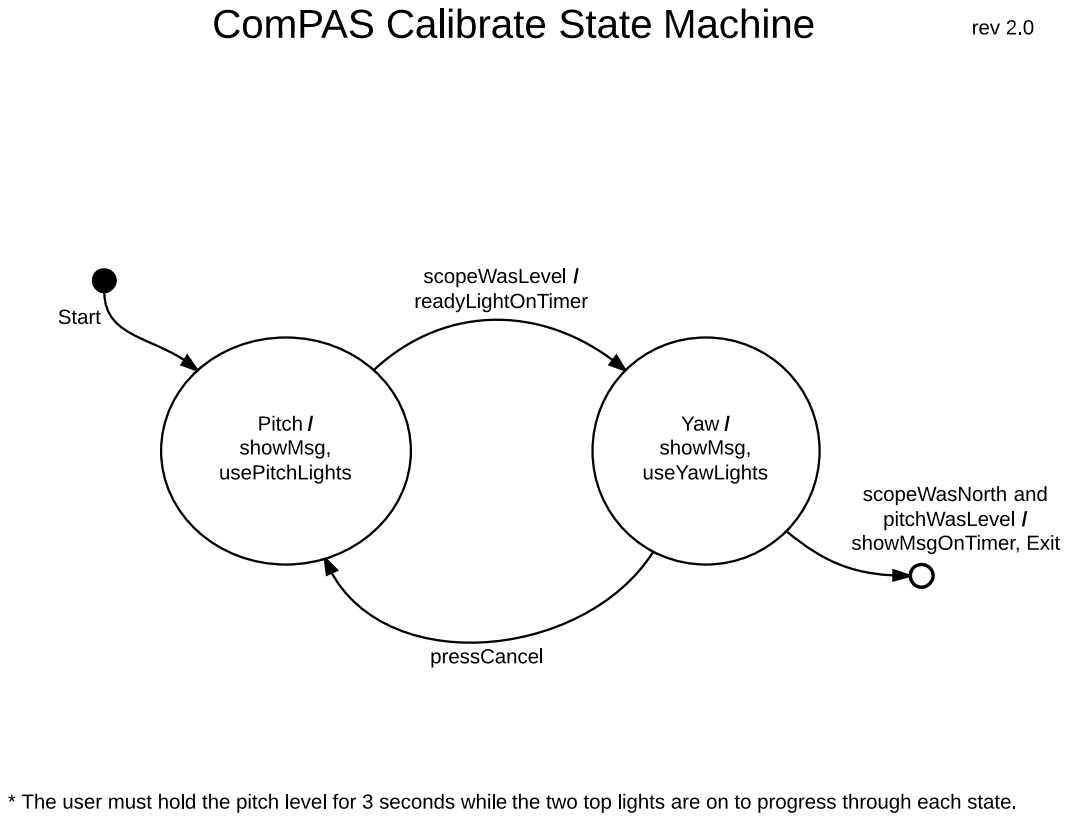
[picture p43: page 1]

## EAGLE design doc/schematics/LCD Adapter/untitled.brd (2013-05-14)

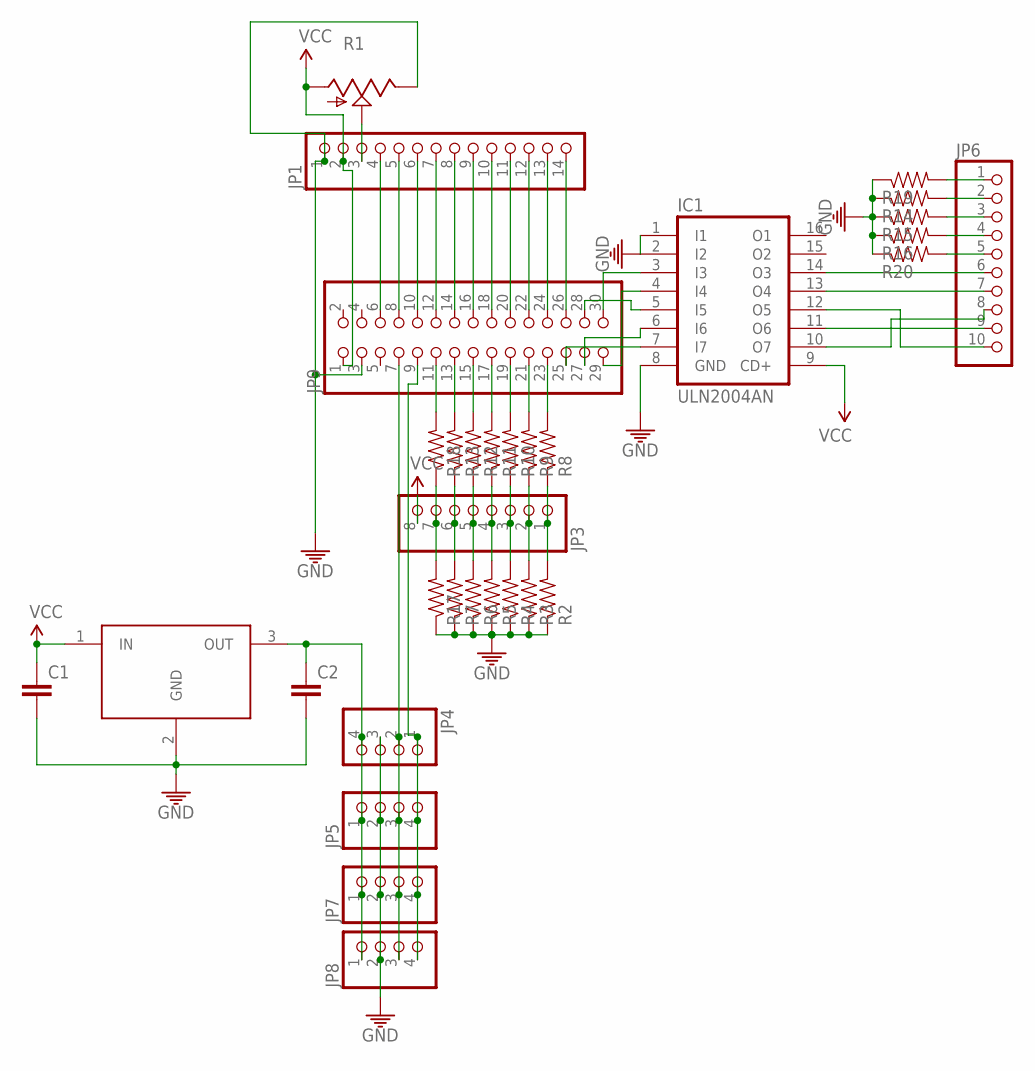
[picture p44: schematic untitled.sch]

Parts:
C1, C2: CAP0805; 0805
IC1: ULN2004AN; DIL16
JP1: PINHD-1X14; 1X14
JP3: PINHD-1X8/90; 1X08/90
JP4, JP5, JP7, JP8: PINHD-1X4; 1X04
JP6: PINHD-1X10; 1X10
JP9: PINHD-2X15/90; 2X15/90
R1: TRIM_US-B90P; SP19L
R2, R3, R4, R5, R6, R7, R8, R9, R10, R11, R12, R13, R14, R15, R16, R17, R18, R19, R20: RESISTOR0805-RES; 0805
U$5: LM3940IMP-3.3; SOT223

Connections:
3.3V: C2.1, JP4.4, JP5.1, JP7.1, JP8.1, U$5.3 (OUT)
GND: C1.2, C2.2, IC1.1 (I1), IC1.2 (I2), IC1.8 (GND), JP1.1, JP4.3, JP5.2, JP7.2, JP8.2, JP9.3, R1.E, R2.1, R3.1, R4.1, R5.1, R6.1, R7.1, R14.1, R15.1, R16.1, R17.1, R19.1, R20.1, U$5.2 (GND)
unnamed: JP1.3, R1.S
unnamed: JP3.1, R2.2, R8.1
unnamed: JP3.2, R3.2, R9.1
unnamed: JP1.4, JP9.6
unnamed: JP1.5, JP9.8
unnamed: JP1.6, JP9.10
unnamed: JP1.7, JP9.12
unnamed: JP4.1, JP5.4, JP7.4, JP8.4, JP9.9
unnamed: JP1.8, JP9.14
unnamed: JP1.9, JP9.16
unnamed: JP1.10, JP9.18
unnamed: JP1.11, JP9.20
unnamed: JP1.12, JP9.22
unnamed: JP1.13, JP9.24
unnamed: JP3.3, R4.2, R10.1
unnamed: JP3.4, R5.2, R11.1
unnamed: JP3.5, R6.2, R12.1
unnamed: JP3.6, R7.2, R13.1
unnamed: JP9.13, R13.2
unnamed: JP9.15, R12.2
unnamed: JP9.17, R11.2
unnamed: JP9.19, R10.2
unnamed: JP9.21, R9.2
unnamed: JP9.23, R8.2
unnamed: JP1.14, JP9.26
unnamed: JP3.7, R17.2, R18.1
unnamed: IC1.7 (I7), JP9.25
unnamed: JP6.2, R14.2
unnamed: JP6.3, R15.2
unnamed: JP6.4, R16.2
unnamed: IC1.12 (O5), JP6.10
unnamed: IC1.5 (I5), JP9.28
unnamed: JP4.2, JP5.3, JP7.3, JP8.3, JP9.7
unnamed: JP9.11, R18.2
unnamed: JP6.1, R19.2
unnamed: JP6.5, R20.2
unnamed: IC1.4 (I4), JP9.29
unnamed: IC1.3 (I3), JP9.30
unnamed: IC1.10 (O7), JP6.8
unnamed: IC1.11 (O6), JP6.9
unnamed: IC1.13 (O4), JP6.7
unnamed: IC1.14 (O3), JP6.6
unnamed: IC1.6 (I6), JP9.27
VCC: C1.1, IC1.9 (CD+), JP1.2, JP3.8, JP9.1, R1.A, U$5.1 (IN)

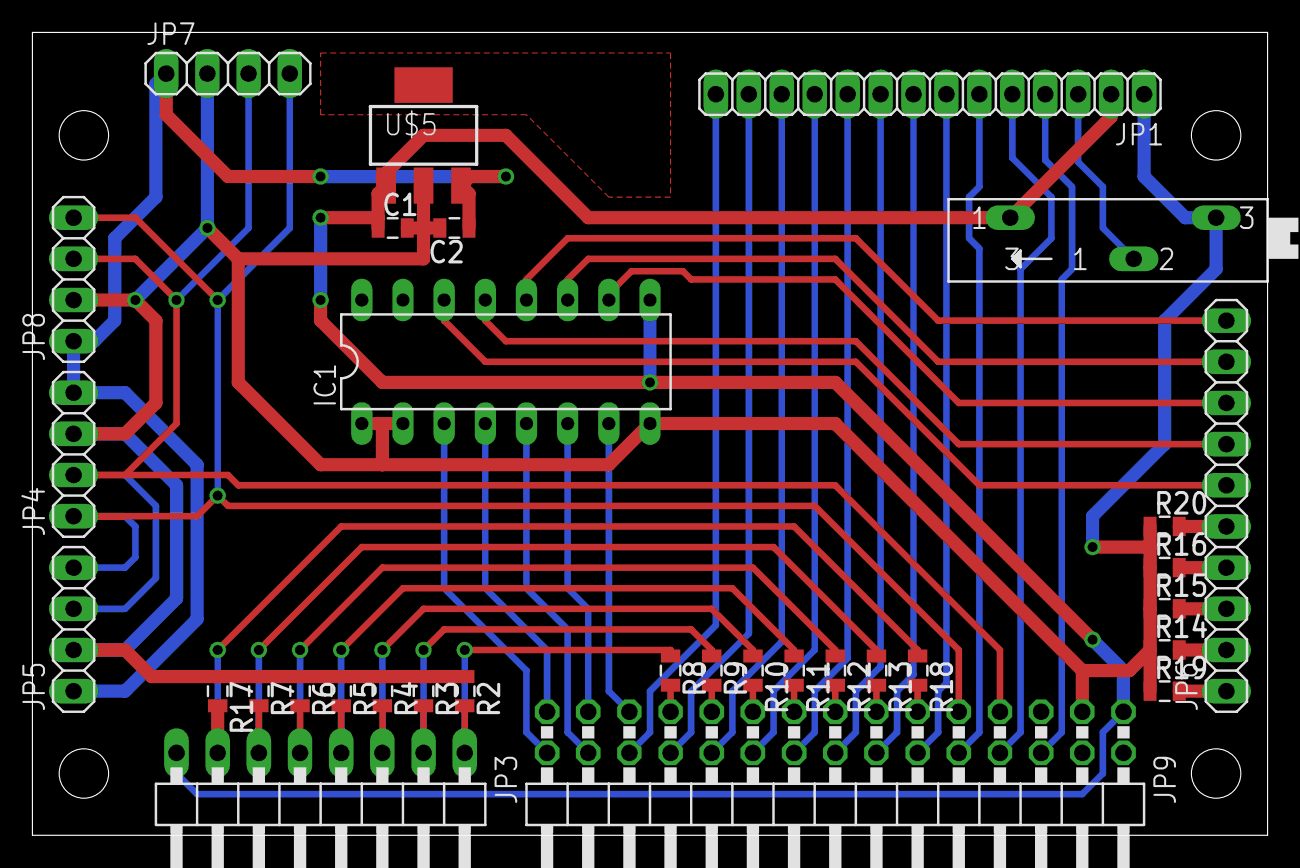
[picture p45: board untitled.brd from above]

Board: 2 copper layers, 76.2 x 49.5 mm, 36 parts (0 on the bottom side), 46 nets.

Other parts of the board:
U$1, U$2, U$3, U$4: STAND-OFF-TIGHT

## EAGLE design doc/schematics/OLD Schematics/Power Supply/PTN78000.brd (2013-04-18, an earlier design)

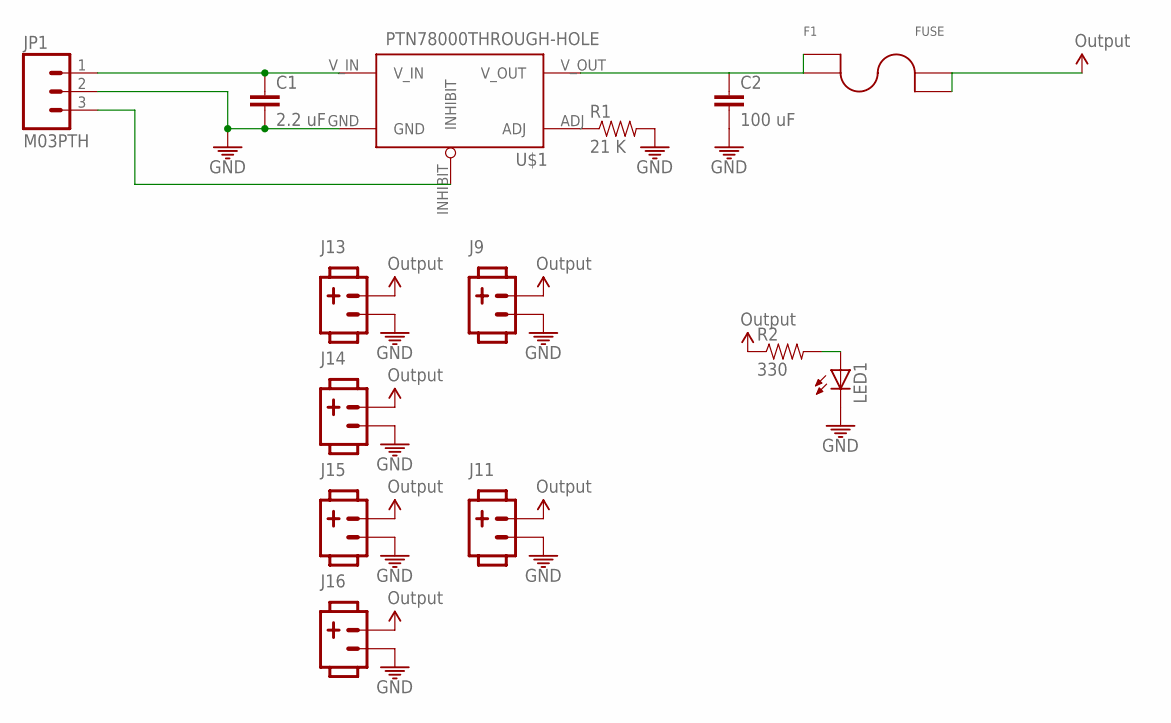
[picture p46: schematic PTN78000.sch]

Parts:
C1: 2.2 uF; 1206
C2: 100 uF; 1206
F1: FUSE; FUSE_2AG
J9, J11, J13, J14, J15, J16: POW_CONNECTFEMALE-RA; SOCKET-FEMALE_RA-3.96MM-2
JP1: M03PTH; 1X03
LED1: LED5MM
R1: 21 K; 1206
R2: 330; 1206
U$1: PTN78000THROUGH-HOLE; PTN78000

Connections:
GND: C1.2, C2.2, J9.2, J11.2, J13.2, J14.2, J15.2, J16.2, JP1.2, LED1.K (C), R1.2, U$1.GND
unnamed: C1.1, JP1.1, U$1.V_IN
unnamed: R1.1, U$1.ADJ
unnamed: JP1.3, U$1.INHIBIT
unnamed: C2.1, F1.P$1 (1), F1.P$2 (2), U$1.V_OUT
unnamed: LED1.A, R2.2
VCC5V0: F1.P$3 (3), F1.P$4 (4), J9.1, J11.1, J13.1, J14.1, J15.1, J16.1, R2.1

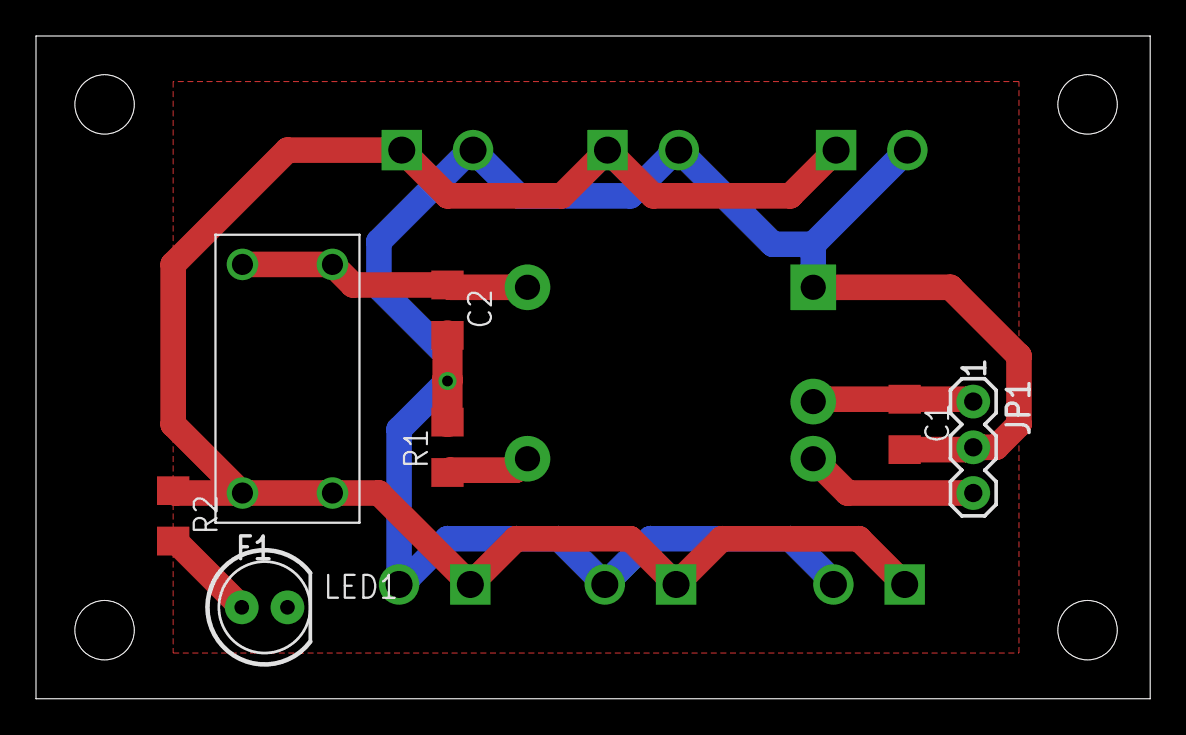
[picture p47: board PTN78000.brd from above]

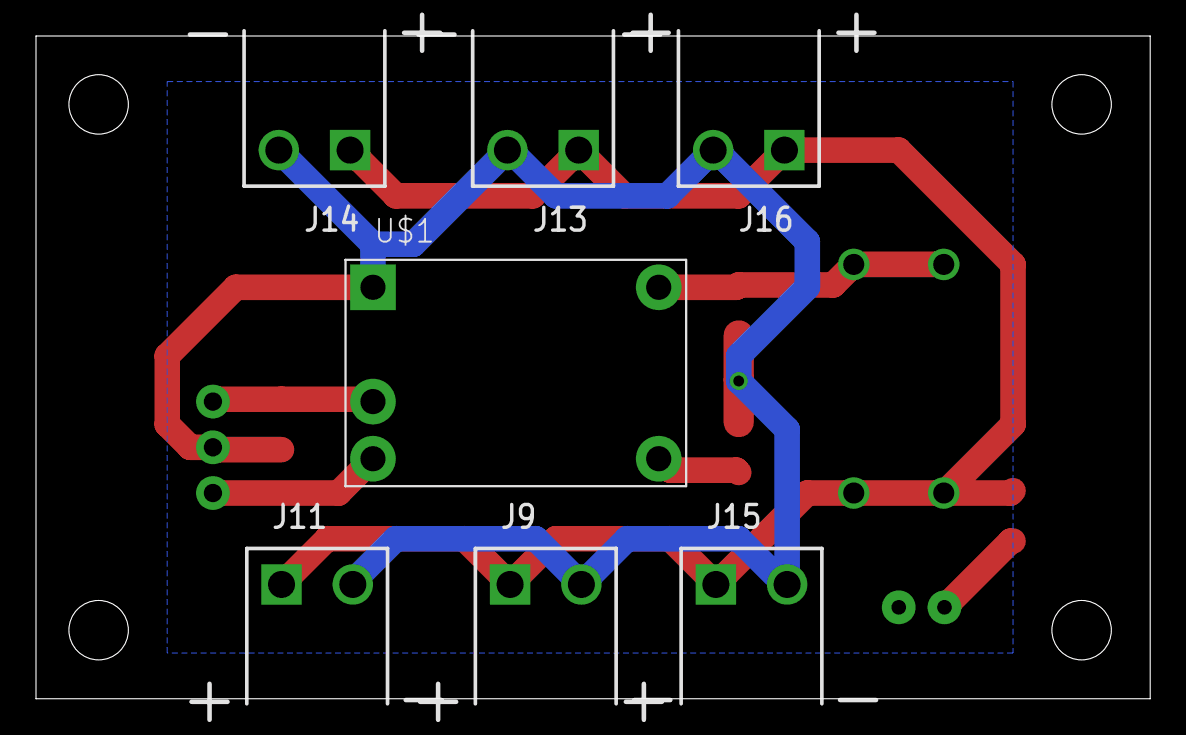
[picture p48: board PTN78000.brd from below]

Board: 2 copper layers, 61.9 x 36.8 mm, 18 parts (7 on the bottom side), 7 nets.

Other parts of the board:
U$6, U$11, U$12, U$13: STAND-OFF

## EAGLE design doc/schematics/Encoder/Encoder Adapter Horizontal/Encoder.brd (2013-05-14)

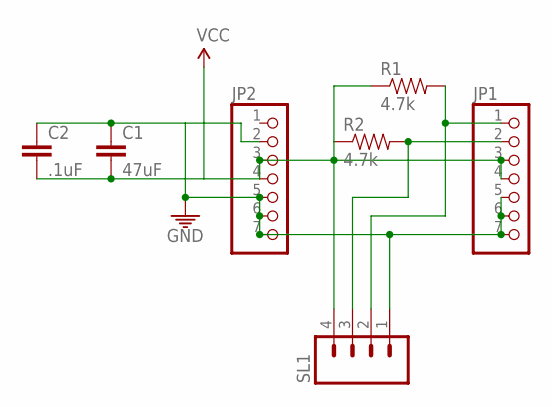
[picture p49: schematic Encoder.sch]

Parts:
C1: 47uF; 0805
C2: .1uF; 0805
JP1, JP2: PINHD-1X7; 1X07
R1, R2: 4.7k; 0805
SL1: M04LOCK; 1X04_LOCK

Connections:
GND: C1.1, C2.1, JP1.5, JP1.6, JP1.7, JP2.2, JP2.5, JP2.6, JP2.7, SL1.1
unnamed: JP1.1, R1.2, SL1.2
unnamed: JP1.2, R2.2, SL1.3
VCC: C1.2, C2.2, JP1.3, JP1.4, JP2.3, JP2.4, R1.1, R2.1, SL1.4

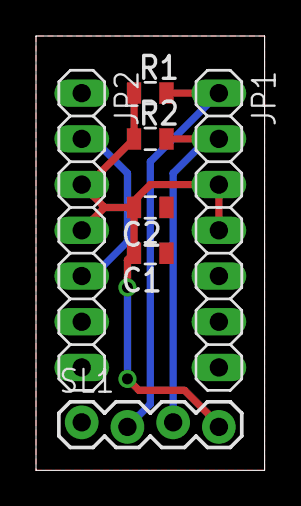
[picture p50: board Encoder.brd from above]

Board: 2 copper layers, 12.7 x 24.1 mm, 7 parts (0 on the bottom side), 4 nets.

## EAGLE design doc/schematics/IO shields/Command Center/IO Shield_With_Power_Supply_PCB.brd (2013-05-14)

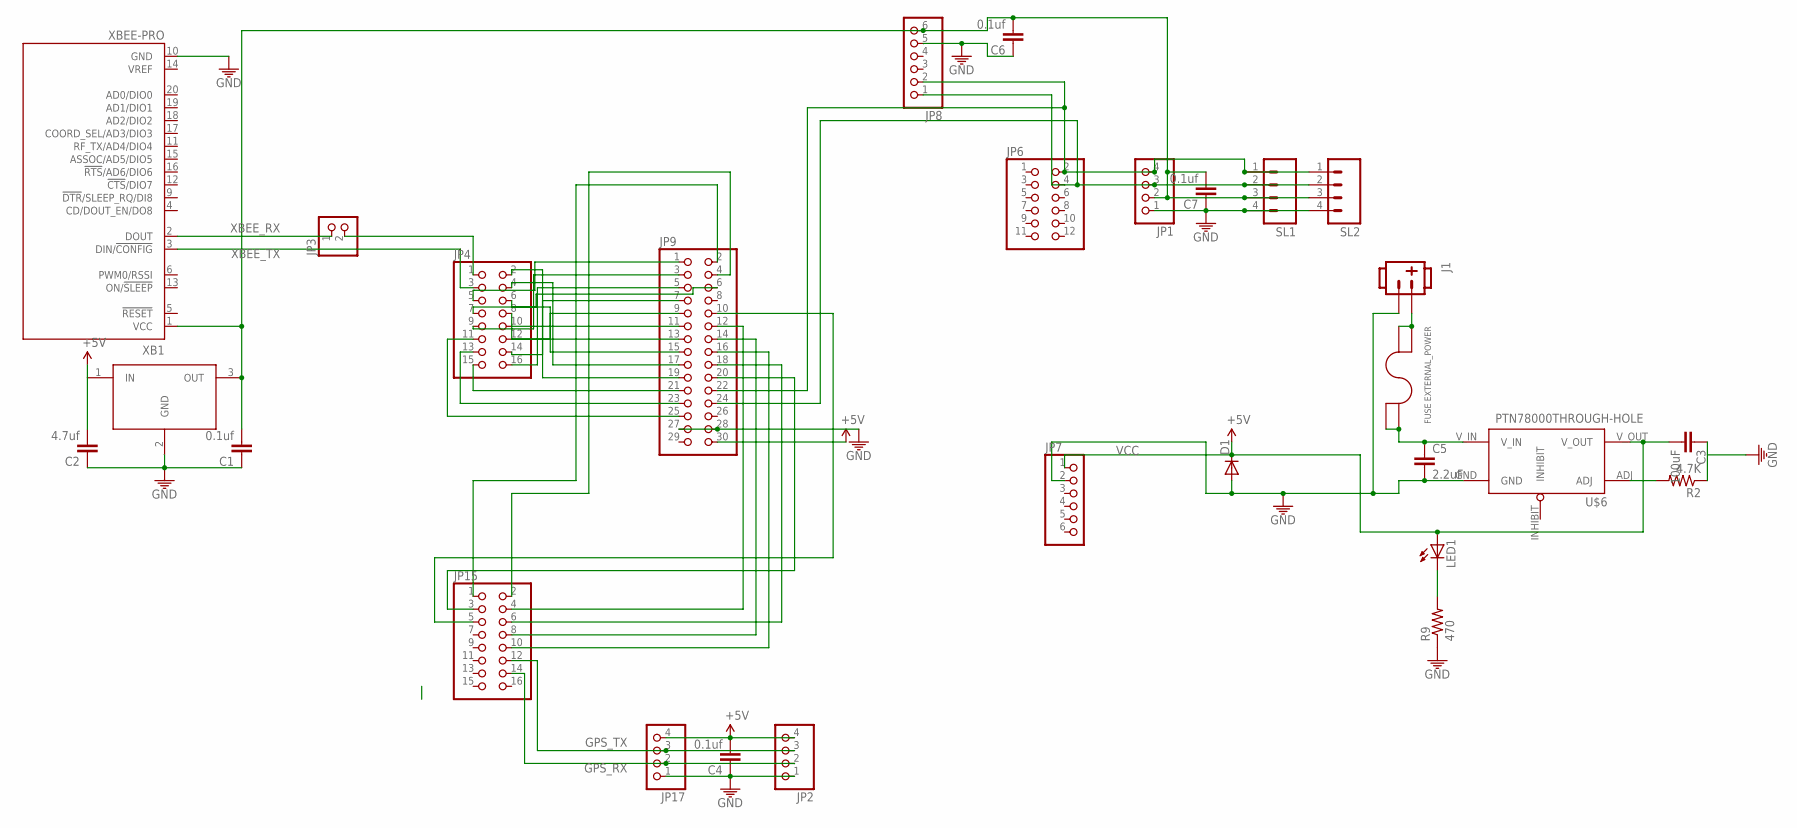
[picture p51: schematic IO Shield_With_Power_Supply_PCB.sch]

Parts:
C1, C4, C6, C7: 0.1uf; C0805
C2: 4.7uf; C0805
C3: 100uF; C0805
C5: 2.2uF; C0805
D1: DIODEPTH; DIODE-1N4001
EXTERNAL_POWER: FUSE; FUSE_2AG
J1: POW_CONNECTMALE; SOCKET-MALE-3.96MM-2
JP1, JP17: PINHD-1X4; 1X04
JP2: PINHD-1X4/90; 1X04/90
JP3: PINHD-1X2; 1X02
JP4, JP15: PINHD-2X8; 2X08
JP6: PINHD-2X6; 2X06
JP7, JP8: PINHD-1X6; 1X06
JP9: PINHD-2X15/90; 2X15/90
LED1: LED-FKIT-1206; FKIT-LED-1206
R2: 4.7K; 0805
R9: 470; 0805
SL1, SL2: M04LOCK; 1X04_LOCK
U$6: PTN78000THROUGH-HOLE; PTN78000
U$7: LM3940IMP-3.3; SOT223
XB1: XBEE-PRO

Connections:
GND: C1.1, C2.1, C3.1, C4.1, C5.2, C6.1, C7.1, D1.A, J1.P$2 (2), JP1.1, JP2.1, JP7.2, JP8.5, JP9.27, JP9.28, JP17.1, R2.1, R9.1, SL1.4, SL2.4, U$6.GND, U$7.2 (GND), XB1.10 (GND)
GPS_RX: JP2.2, JP15.14, JP17.2
GPS_TX: JP2.3, JP15.12, JP17.3
unnamed: JP3.1, XB1.2 (DOUT)
unnamed: JP4.5, JP9.1
unnamed: EXTERNAL_POWER.P$1 (1), EXTERNAL_POWER.P$2 (2), J1.P$1 (1)
unnamed: JP4.9, JP9.3
unnamed: JP4.7, JP9.6
unnamed: JP9.2, JP15.1
unnamed: JP9.4, JP15.2
unnamed: JP4.16, JP9.5
unnamed: JP4.14, JP9.7
unnamed: JP4.12, JP9.9
unnamed: JP9.10, JP15.5
unnamed: JP4.10, JP9.11
unnamed: C1.2, C6.2, C7.2, JP1.2, JP8.6, SL1.3, SL2.3, U$7.3 (OUT), XB1.1 (VCC)
unnamed: JP4.8, JP9.13
unnamed: C5.1, EXTERNAL_POWER.P$3 (3), EXTERNAL_POWER.P$4 (4), U$6.V_IN
unnamed: JP4.6, JP9.15
unnamed: JP4.4, JP9.17
unnamed: JP4.2, JP9.19
unnamed: JP4.15, JP9.21
unnamed: JP4.13, JP9.23
unnamed: JP4.11, JP9.25
unnamed: JP9.14, JP15.8
unnamed: JP9.18, JP15.6
unnamed: LED1.C, R9.2
unnamed: JP1.4, JP6.2, JP8.2, JP9.22, SL1.1, SL2.1
unnamed: JP9.16, JP15.10
unnamed: JP9.12, JP15.4
unnamed: JP9.20, JP15.3
unnamed: R2.2, U$6.ADJ
unnamed: JP1.3, JP6.4, JP8.1, JP9.24, SL1.2, SL2.2
VCC: C2.2, C3.2, C4.2, D1.C, JP2.4, JP7.1, JP9.30, JP17.4, LED1.A, U$6.V_OUT, U$7.1 (IN)
XBEE_RX: JP3.2, JP4.1
XBEE_TX: JP4.3, XB1.3 (DIN/!CONFIG)

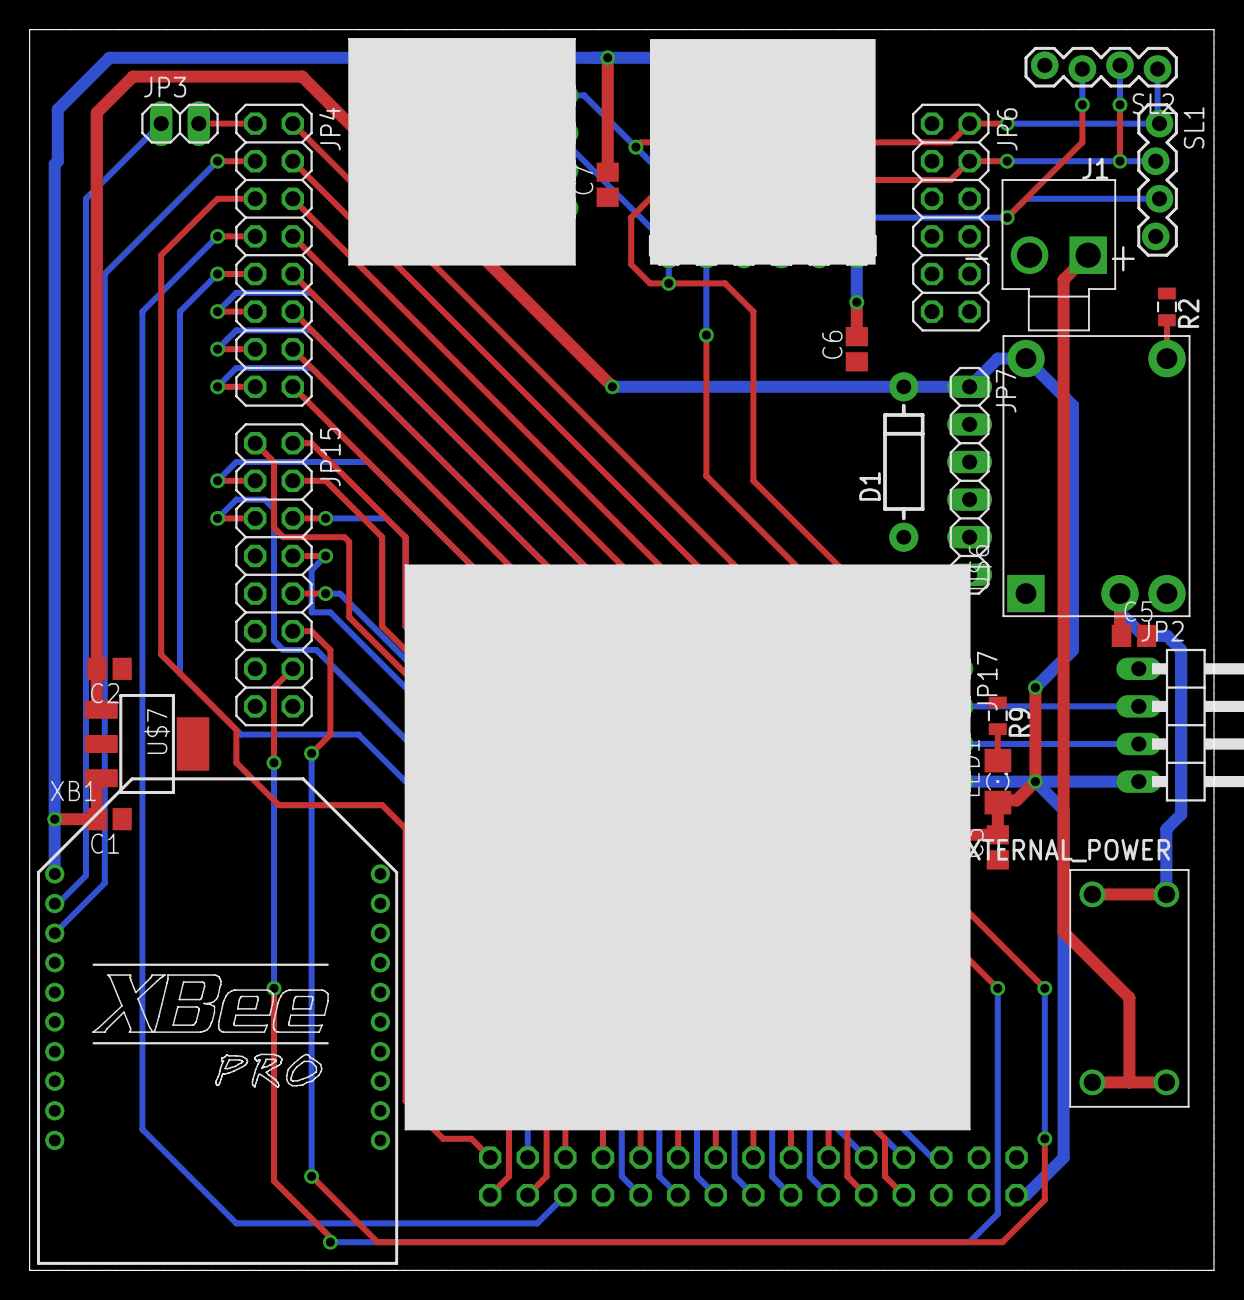
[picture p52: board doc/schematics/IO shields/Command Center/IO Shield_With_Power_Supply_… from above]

Board: 2 copper layers, 80.0 x 83.8 mm, 32 parts (1 on the bottom side), 36 nets.

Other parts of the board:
U$2, U$3, U$4, U$5: STAND-OFF

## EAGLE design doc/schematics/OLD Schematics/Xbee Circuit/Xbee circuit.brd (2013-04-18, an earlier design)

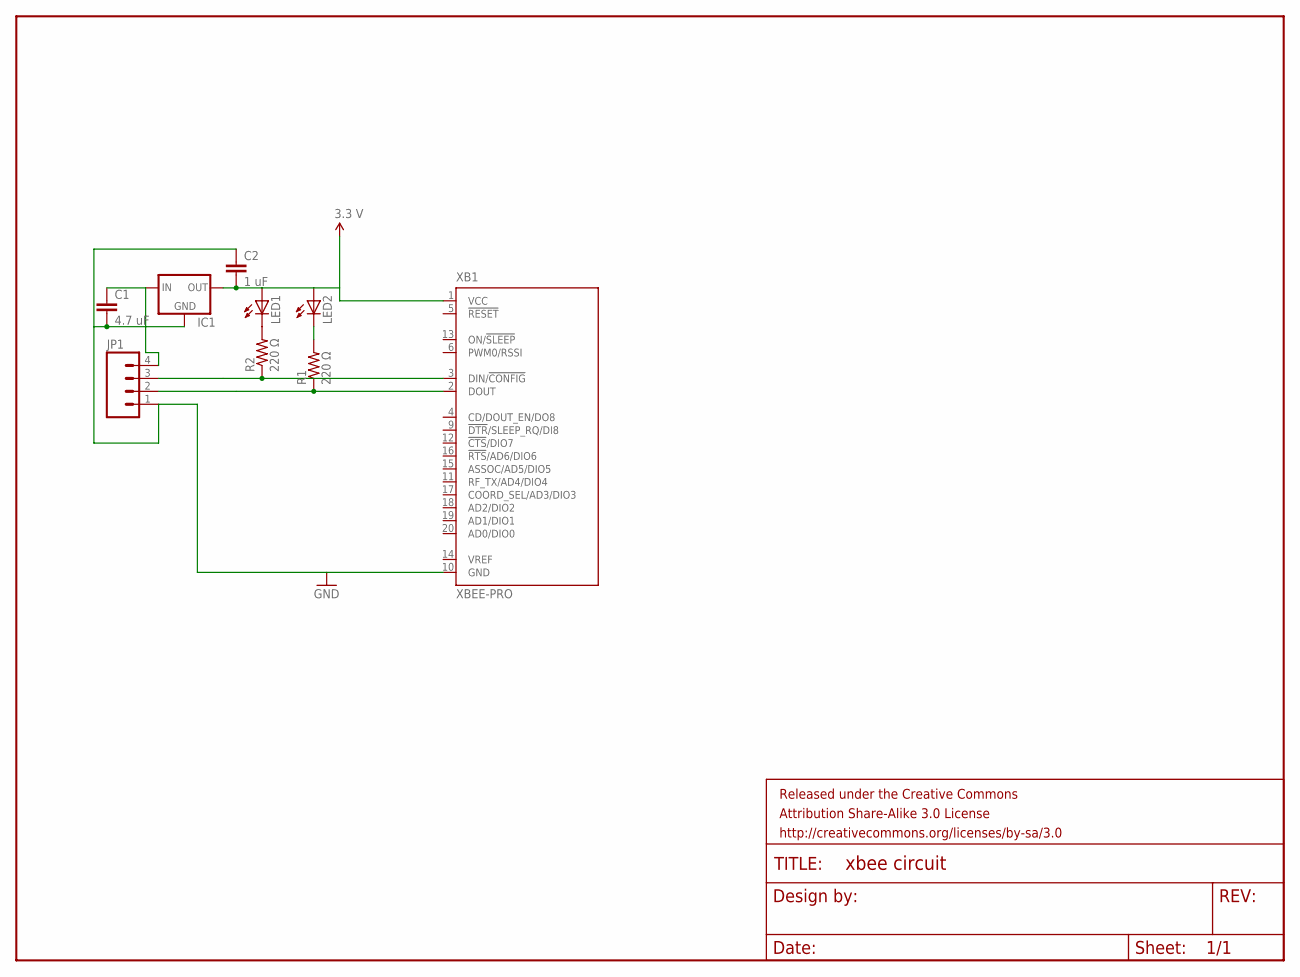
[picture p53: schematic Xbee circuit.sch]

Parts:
C1: 4.7 uF; 0805
C2: 1 uF; 0805
FRAME1: FRAME-LETTER; CREATIVE_COMMONS
IC1: V_REG_78XXSINK; TO220-IGO
JP1: M04LOCK; 1X04_LOCK
LED1, LED2: LED5MM
R1, R2: 220 Ω; 0805
XB1: XBEE-PRO

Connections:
GND: C1.2, C2.1, IC1.GND, JP1.1, XB1.10 (GND)
unnamed: LED2.K (C), R1.2
unnamed: LED1.K (C), R2.2
unnamed: JP1.3, R2.1, XB1.3 (DIN/!CONFIG)
unnamed: JP1.2, R1.1, XB1.2 (DOUT)
unnamed: C1.1, IC1.IN, JP1.4
VCC: C2.2, IC1.OUT, LED1.A, LED2.A, XB1.1 (VCC)

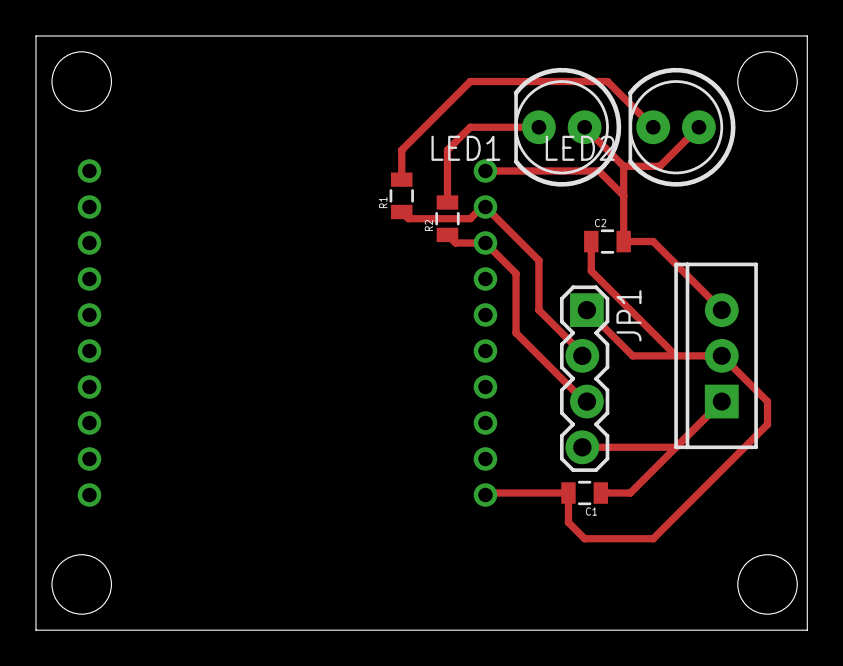
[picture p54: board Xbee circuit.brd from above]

Board: 2 copper layers, 42.9 x 33.0 mm, 14 parts (1 on the bottom side), 7 nets.

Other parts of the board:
U$1, U$2, U$3, U$4: STAND-OFF

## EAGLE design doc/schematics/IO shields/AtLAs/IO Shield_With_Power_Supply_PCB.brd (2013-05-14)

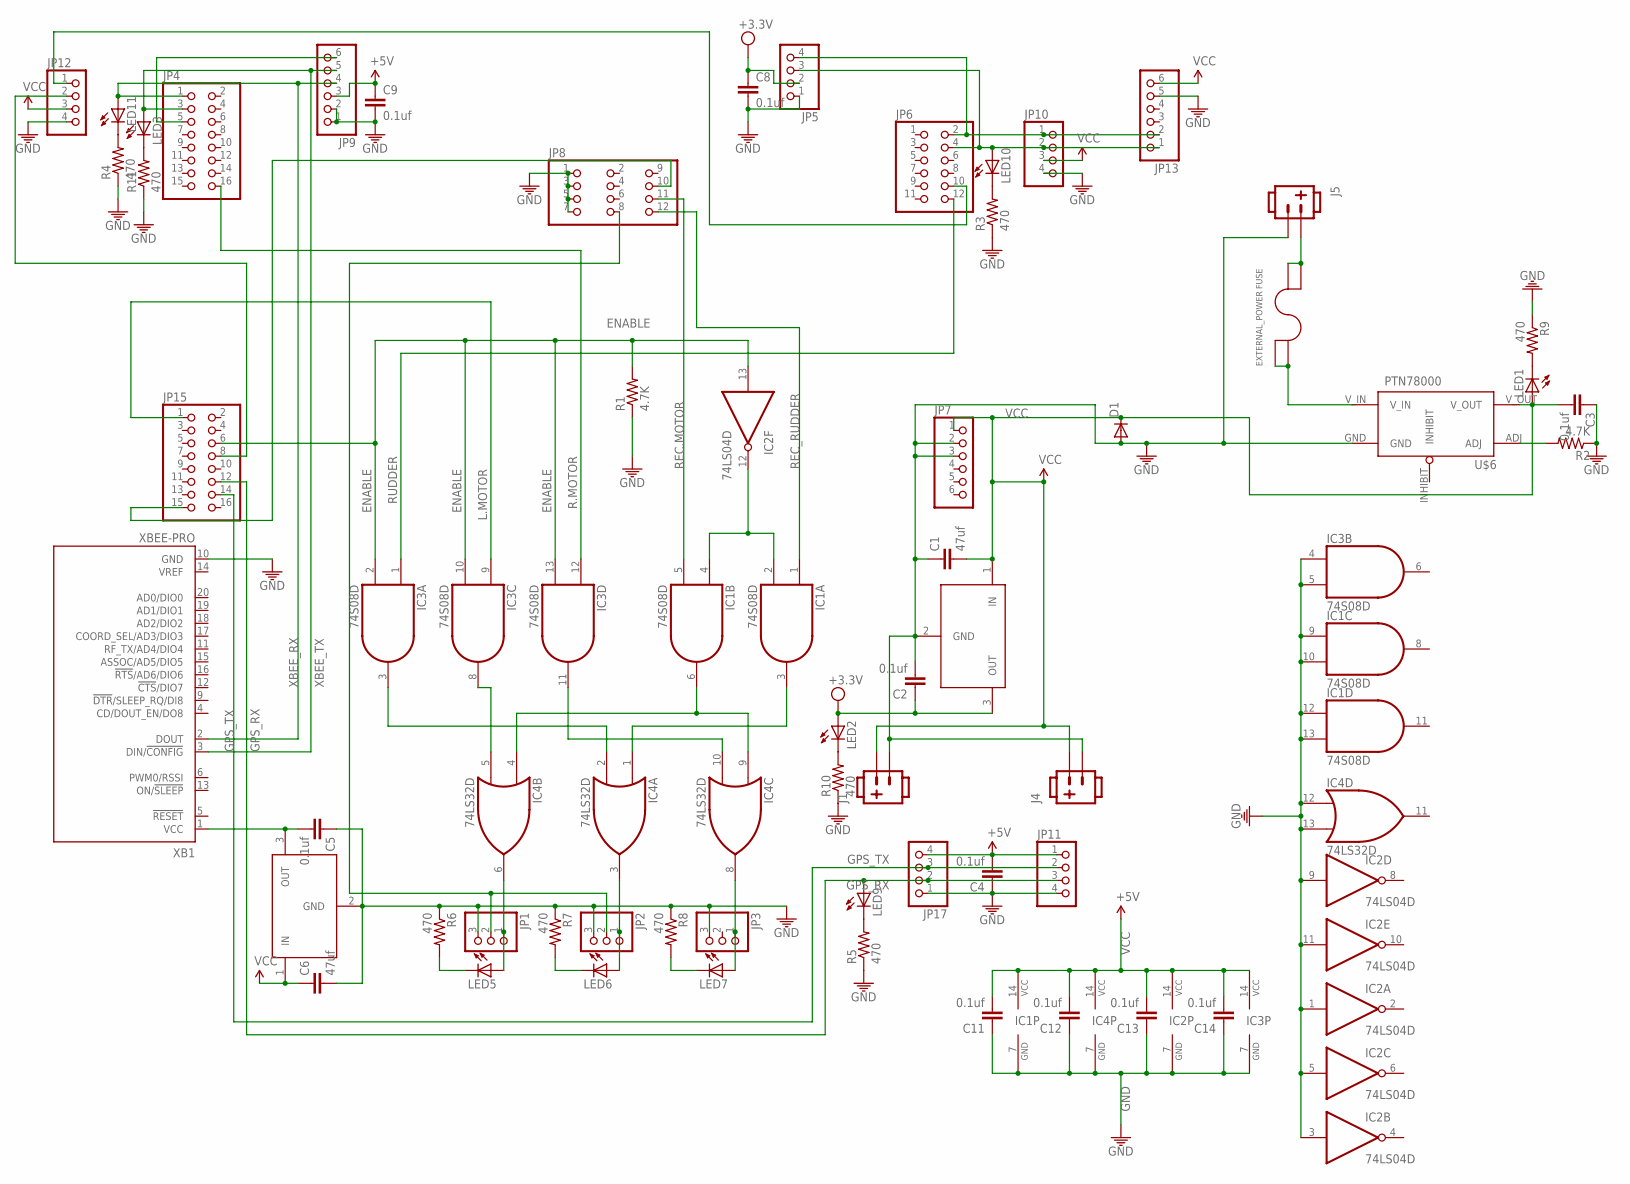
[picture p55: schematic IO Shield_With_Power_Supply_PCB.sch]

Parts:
C1, C6: 47uf; C0805
C2, C3, C4, C5, C8, C9, C11, C12, C13, C14: 0.1uf; C0805
D1: DIODEPTH; DIODE-1N4001
EXTERNAL_POWER: FUSE; FUSE_2AG
IC1, IC3: 74S08D; SO14
IC2: 74LS04D; SO14
IC4: 74LS32D; SO14
J1, J4, J5: POW_CONNECTFEMALE-RA; SOCKET-FEMALE_RA-3.96MM-2
JP1, JP2, JP3: PINHD-1X3/90; 1X03/90
JP4, JP15: PINHD-2X8; 2X08
JP5, JP17: PINHD-1X4; 1X04
JP6: PINHD-2X6; 2X06
JP7: PINHD-1X6; 1X06@1
JP8: PINHD-2X4; 2X04
JP9, JP13: PINHD-1X6; 1X06
JP10, JP11, JP12: PINHD-1X4/90; 1X04/90
LED1, LED2, LED3, LED5, LED6, LED7, LED9, LED10, LED11: LED-FKIT-1206; FKIT-LED-1206
R1, R2: 4.7K; 0805
R3, R4, R5, R6, R7, R8, R9, R10, R11: 470; 0805
U$1, U$7: LM3940IMP-3.3; SOT223
U$6: PTN78000
XB1: XBEE-PRO

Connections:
ENABLE: IC2.13 (I), IC3.2 (I1), IC3.10 (I1), IC3.13 (I1), JP15.6, R1.2
GND: C1.1, C2.2, C3.1, C4.1, C5.1, C6.2, C8.2, C9.2, C11.1, C12.1, C13.1, C14.1, D1.A, IC1.7 (GND), IC1.9 (I0), IC1.10 (I1), IC1.12 (I0), IC1.13 (I1), IC2.1 (I), IC2.3 (I), IC2.5 (I), IC2.7 (GND), IC2.9 (I), IC2.11 (I), IC3.4 (I0), IC3.5 (I1), IC3.7 (GND), IC4.7 (GND), IC4.12 (I0), IC4.13 (I1), J1.2, J4.2, J5.2, JP1.3, JP2.3, JP3.3, JP5.1, JP7.2, JP7.3, JP8.1, JP8.3, JP8.5, JP8.7, JP9.1, JP9.2, JP10.4, JP11.4, JP12.4, JP13.5, JP17.1, R1.1, R2.1, R3.1, R4.1, R5.1, R6.1, R7.1, R8.1, R9.1, R10.1, R11.1, U$1.2 (GND), U$6.GND, U$7.2 (GND), XB1.10 (GND)
GPS_RX: JP11.3, JP15.12, JP17.2, LED9.A
GPS_TX: JP11.2, JP15.14, JP17.3
L.MOTOR: IC3.9 (I0), JP15.1
unnamed: IC1.3 (O), IC4.1 (I0)
unnamed: IC1.6 (O), IC4.4 (I0), IC4.9 (I0)
unnamed: IC1.2 (I1), IC1.4 (I0), IC2.12 (O)
unnamed: JP6.10, JP12.1
unnamed: IC3.11 (O), IC4.10 (I1)
unnamed: IC3.8 (O), IC4.5 (I1)
unnamed: JP12.2, JP15.8
unnamed: IC4.6 (O), JP1.1, LED5.A
unnamed: IC4.3 (O), JP2.1, LED6.A
unnamed: IC4.8 (O), JP3.1, LED7.A
unnamed: JP1.2, JP2.2, JP8.8
unnamed: EXTERNAL_POWER.P$1 (1), EXTERNAL_POWER.P$2 (2), U$6.V_IN
unnamed: JP8.10 (9), JP15.15
unnamed: C5.2, U$7.3 (OUT), XB1.1 (VCC)
unnamed: LED3.C, R11.2
unnamed: JP4.5, JP9.6
unnamed: LED10.C, R3.2
unnamed: LED11.C, R4.2
unnamed: LED9.C, R5.2
unnamed: LED5.C, R6.2
unnamed: LED6.C, R7.2
unnamed: LED7.C, R8.2
unnamed: LED1.C, R9.2
unnamed: LED2.C, R10.2
unnamed: IC3.3 (O), IC4.2 (I1)
unnamed: EXTERNAL_POWER.P$3 (3), EXTERNAL_POWER.P$4 (4), J5.1
unnamed: R2.2, U$6.ADJ
R.MOTOR: IC3.12 (I0), JP4.16
REC.MOTOR: IC1.5 (I1), JP8.11
REC_RUDDER: IC1.1 (I0), JP8.12
RUDDER: IC3.1 (I0), JP6.12
SCL: JP5.4, JP6.2, JP10.1, JP13.2
SDA: JP5.3, JP6.4, JP10.2, JP13.1, LED10.A
VCC: C1.2, C3.2, C4.2, C6.1, C9.1, C11.2, C12.2, C13.2, C14.2, D1.C, IC1.14 (VCC), IC2.14 (VCC), IC3.14 (VCC), IC4.14 (VCC), J1.1, J4.1, JP7.1, JP9.3, JP10.3, JP11.1, JP12.3, JP13.6, JP17.4, LED1.A, U$1.1 (IN), U$6.V_OUT, U$7.1 (IN)
VDD: C2.1, C8.1, JP5.2, LED2.A, U$1.3 (OUT)
XBEE_RX: JP4.1, JP9.4, LED11.A, XB1.2 (DOUT)
XBEE_TX: JP4.3, JP9.5, LED3.A, XB1.3 (DIN/!CONFIG)



Board: 2 copper layers, 78.7 x 83.8 mm, 64 parts (5 on the bottom side), 42 nets.

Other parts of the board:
U$2, U$3, U$4, U$5: STAND-OFF

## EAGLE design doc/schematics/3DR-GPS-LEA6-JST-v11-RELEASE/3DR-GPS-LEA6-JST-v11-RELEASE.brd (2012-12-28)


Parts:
C1, C6, C10: 0.1uF; 0402-CAP
C2, C3: 4.7uF; 0805
C4: 0.01uF; 0402-CAP
C5: 470pF; 0402-CAP
C7: 33nF; 0402-CAP
C8, C9: 8.2pF; 0402-CAP
D1: RB751V40T1G; SOD-323
D2: MMSZ5233BT1GOSTR; SOD-123
F1: MF-PSMF050X-2; 0805
JP1, JP2: FIDUCIAL1X2; FIDUCIAL-1X2
JP3, JP4, JP5, JP6: STAND-OFF
L3: 6.8nH; C0402
L5: 27nH; C0402
L6: BKP1005HS121-T; 0402-IND
L7, L8: BLM15HD102SN1; 0402-IND
LED1: RED; LED-0603
LED2: BLUE; LED-0603
R1: 1k; 0402-RES
R2, R3: 330; 0402-RES
TP1, TP2, TP3, TP4: TPTP20SQ; TP20SQ
U1: TPS79133DBV; SOT23-5
U$1: UBLOX-LEA-6
U$5: 24AA32A; SOT23-5
U$6: MAX2659; UDFN-6
U$7: B7839; QCS5E
U$8: MS621FE
U$9: GP.1575.25.4.A.02
X1: SM06B-SRSS-TB

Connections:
3.3V: C2.1, C3.1, C6.1, D1.2 (A), R2.2, U1.5 (OUT), U$1.6 (VCC), U$5.4 (VCC)
5V: C1.1, D2.C, L6.1, U1.1 (IN)
5V_RAW: F1.2, TP1.TP, X1.5
GND: C1.2, C2.2, C3.2, C4.2, C6.2, C7.1, C10.1, D2.A, LED1.C, LED2.C, TP4.TP, U1.2 (GND), U1.3 (EN), U$1.7 (GND1), U$1.13 (GND2), U$1.14 (GND3), U$1.15 (GND4), U$1.17 (GND5), U$5.2 (GND), U$5.5 (WP), U$6.1 (GND1), U$6.2 (GND2), U$7.2 (GND1), U$7.3 (GND2), U$7.5 (GND3), U$8.2 (NEG), X1.2, X1.6
unnamed: L3.2, U$6.3 (RFIN)
unnamed: C4.1, U1.4 (BP)
unnamed: C5.2, L3.1
unnamed: C8.2, U$7.4 (IN)
unnamed: R3.1, U$1.28 (TIMEPULSE)
unnamed: C9.1, U$7.1 (OUT)
unnamed: C7.2, U$1.18 (VCC_RF), U$1.19 (V_ANT), U$6.4 (VCC)
unnamed: C8.1, U$6.6 (RFOUT)
unnamed: C10.2, L5.1, U$6.5 (!SHDN)
unnamed: C5.1, U$9.1
unnamed: C9.2, L5.2, U$1.16 (RF_IN)
unnamed: D1.1 (C), R1.2
unnamed: LED1.A, R2.1
unnamed: LED2.A, R3.2
unnamed: F1.1, L6.2
RXD1: L8.1, U$1.4 (RXD1)
RX_PAD: L8.2, TP3.TP, X1.4
SCL2: U$1.2 (SCL2/SPI_MISO), U$5.1 (SCL)
SDA2: U$1.1 (SDA2/SPI_MOSI), U$5.3 (SDA)
TXD1: L7.1, U$1.3 (TXD1)
TX_PAD: L7.2, TP2.TP, X1.3
VBAT: R1.1, U$1.11 (V_BCKP), U$8.1 (POS)

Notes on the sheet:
POWER
EEPROM
CONNECTOR



Board: 4 copper layers, 38.1 x 38.1 mm, 41 parts (5 on the bottom side), 26 nets.

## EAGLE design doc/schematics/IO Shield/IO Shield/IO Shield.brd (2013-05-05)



Board: 2 copper layers, 76.2 x 83.8 mm, 40 parts (4 on the bottom side), 64 nets.

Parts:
C1, C3: 47uf; C0805
C2, C4, C8, C9, C10, C11, C12, C13, C14: 0.1uf; C0805
D1: DIODE-1N4001
EXTERNAL_POWER: FUSE; FUSE_2AG
IC1, IC3: 74S08D; SO14
IC2: 74LS04D; SO14
IC4: 74LS32D; SO14
INTERNAL_POWER: FUSE; FUSE_2AG
J1: POW_CONNECTFEMALE-RA; SOCKET-FEMALE_RA-3.96MM-2
JP1, JP2, JP3: 1X03/90
JP4, JP11, JP15, JP16: 2X08
JP5, JP17: 1X04
JP6, JP13: 2X06
JP7, JP9, JP14: 1X06
JP8: 2X04
R1: 4.7K; 0805
U$1: LM3940IMP-3.3; SOT223
U$2, U$3, U$4, U$5: STAND-OFF

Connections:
ENABLE: IC2.13, IC3.2, IC3.10, IC3.13, JP15.6, JP16.6, R1.2
GND: C1.1, C2.2, C3.2, C4.1, C8.2, C9.2, C10.2, C11.1, C12.1, C13.1, C14.1, D1.A, IC1.7, IC1.9, IC1.10, IC1.12, IC1.13, IC2.1, IC2.3, IC2.5, IC2.7, IC2.9, IC2.11, IC3.4, IC3.5, IC3.7, IC4.7, IC4.12, IC4.13, J1.2, JP1.3, JP2.3, JP3.3, JP5.1, JP7.2, JP7.3, JP8.1, JP8.3, JP8.5, JP8.7, JP9.1, JP9.2, JP14.2, JP14.3, JP17.1, R1.1, U$1.2
GPS_RX: JP15.14, JP16.14, JP17.3
GPS_TX: JP15.12, JP16.12, JP17.2
L.MOTOR: IC3.9, JP15.1, JP16.1
unnamed: IC1.3, IC4.1
unnamed: IC1.6, IC4.4, IC4.9
unnamed: IC1.2, IC1.4, IC2.12
unnamed: JP4.1, JP9.4, JP11.1
unnamed: IC3.11, IC4.10
unnamed: IC3.8, IC4.5
unnamed: IC3.3, IC4.2
unnamed: IC4.6, JP1.1
unnamed: IC4.3, JP2.1
unnamed: IC4.8, JP3.1
unnamed: C1.2, D1.C, EXTERNAL_POWER.P$3, EXTERNAL_POWER.P$4, JP7.1, JP14.1, U$1.1
unnamed: JP1.2, JP2.2, JP8.8
unnamed: C3.1, C10.1, EXTERNAL_POWER.P$1, EXTERNAL_POWER.P$2, J1.1
unnamed: JP8.10, JP15.15, JP16.15
unnamed: JP6.1, JP13.1
unnamed: JP4.3, JP9.5, JP11.3
unnamed: JP4.5, JP9.6, JP11.5
unnamed: JP4.7, JP11.7
unnamed: JP4.15, JP11.15
unnamed: JP4.13, JP11.13
unnamed: JP4.11, JP11.11
unnamed: JP4.9, JP11.9
unnamed: JP4.2, JP11.2
unnamed: JP4.4, JP11.4
unnamed: JP4.6, JP11.6
unnamed: JP4.8, JP11.8
unnamed: JP4.14, JP11.14
unnamed: JP4.12, JP11.12
unnamed: JP4.10, JP11.10
unnamed: JP6.3, JP13.3
unnamed: JP15.3, JP16.3
unnamed: JP15.5, JP16.5
unnamed: JP15.7, JP16.7
unnamed: JP15.13, JP16.13
unnamed: JP15.11, JP16.11
unnamed: JP15.9, JP16.9
unnamed: JP15.2, JP16.2
unnamed: JP15.4, JP16.4
unnamed: JP6.5, JP13.5
unnamed: JP15.8, JP16.8
unnamed: INTERNAL_POWER.P$1, INTERNAL_POWER.P$2, JP7.4, JP14.4
unnamed: JP15.10, JP16.10
unnamed: JP6.7, JP13.7
unnamed: JP6.9, JP13.9
unnamed: JP6.11, JP13.11
unnamed: JP5.4, JP6.2, JP13.2
unnamed: JP5.3, JP6.4, JP13.4
unnamed: JP6.6, JP13.6
unnamed: JP6.8, JP13.8
unnamed: JP6.10, JP13.10
unnamed: JP7.5, JP14.5
unnamed: JP7.6, JP14.6
R.MOTOR: IC3.12, JP4.16, JP11.16
REC.MOTOR: IC1.5, JP8.11
REC_ENABLE: JP15.16, JP16.16
REC_RUDDER: IC1.1, JP8.12
RUDDER: IC3.1, JP6.12, JP13.12
VCC: C4.2, C9.1, C11.2, C12.2, C13.2, C14.2, IC1.14, IC2.14, IC3.14, IC4.14, INTERNAL_POWER.P$3, INTERNAL_POWER.P$4, JP9.3, JP17.4
VDD: C2.1, C8.1, JP5.2, U$1.3

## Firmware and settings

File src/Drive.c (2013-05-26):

/*
 * File:   Drive.c
 * Author: 
 *	David Goodman
 *	Darrel Deo
 *
 * Created on March 27, 2013, 12:34 PM
 */

#include <xc.h>
#include <stdio.h>
#include <plib.h>
#include <math.h>
#include "Drive.h"
#include "Timer.h"
#include "Board.h"
#include "RCServo.h"
#include "Ports.h"
#include "GPS.h"
#include "Drive.h"
#include "I2C.h"
#include "TiltCompass.h"


/***********************************************************************
 * PRIVATE DEFINITIONS                                                 *
 ***********************************************************************/

//#define DEBUG
//#define DEBUG_VERBOSE
//#define DISABLE_MOTORS
#define USE_PUBLIC_DEBUG

#ifdef DEBUG
#ifdef USE_SD_LOGGER
#define DBPRINT(...)   do { char debug[255]; sprintf(debug,__VA_ARGS__); } while(0)
#else
#define DBPRINT(...)   printf(__VA_ARGS__)
#endif
#else
#define DBPRINT(...)   ((int)0)
#endif


// --------------------- Acutator ports -----------------------------
#define MOTOR_LEFT              RC_PORTY07  //RD10, J5-01            //RC_PORTW08 // RB2 -- J7-01
#define MOTOR_RIGHT             RC_PORTY06  //RE7,  J6-16            //RC_PORTW07 // RB3 -- J7-02
#define RUDDER                  RC_PORTV03 //RB2, J7-01

// ---------------------- RC Time Definitions -----------------------
#define RC_STOP_PULSE            1500

// Motor limits
#define RC_MOTOR_MAX            1700
#define RC_MOTOR_MIN            1300
#define RC_MOTOR_FORWARD_RANGE  (RC_MOTOR_MAX - RC_STOP_PULSE)
#define RC_MOTOR_REVERSE_RANGE  (RC_STOP_PULSE - RC_MOTOR_MIN)

// Rudder limits
#define RUDDER_ANGLE_MAX        45.0f // (degree) max rudder angle in either direction
#define RC_RUDDER_MAX           2000
#define RC_RUDDER_MIN           1000
#define RC_RUDDER_LEFT_MAX      RC_RUDDER_MAX
#define RC_RUDDER_RIGHT_MAX     RC_RUDDER_MIN
#define RC_RUDDER_RANGE         (RC_RUDDER_MAX - RC_STOP_PULSE) // left/right dynamic range

// Convert speed (0 to 100%) to RC time
#define MOTOR_PERCENT_TO_RCPULSE(s)           (((uint16_t)RC_MOTOR_FORWARD_RANGE/100)*s + RC_STOP_PULSE)
#define MOTOR_PERCENT_TO_RCPULSE_REVERSE(s)   (((uint16_t)RC_MOTOR_REVERSE_RANGE/100)*s + RC_STOP_PULSE)

// Convert rudder angle to RC time
#define RUDDER_PERCENT_TO_RCPULSE_LEFT(s)     (((uint16_t)RC_RUDDER_RANGE/100)*s + RC_STOP_PULSE)
#define RUDDER_PERCENT_TO_RCPULSE_RIGHT(s)    (-((uint16_t)RC_RUDDER_RANGE/100)*s + RC_STOP_PULSE)


// Delays for control system updating
#define TRACK_UPDATE_DELAY    100 // (ms)

#define DEBUG_PRINT_DELAY   1000 // (ms)

// ------------------------- Controller 
//PD Controller Param Settings for Rudder
#define KP_RUDDER 0.7f
#define KD_RUDDER 0.0f
#define RUDDER_BANGBANG_SPEED_THRESHOLD 45 // (speed %) motor speed threshold
#define RUDDER_BANGBANG_THETA_DEADBAND_THRESHOLD 9 // (degrees) heading error threshold



/***********************************************************************
 * PRIVATE VARIABLES                                                   *
 ***********************************************************************/
static enum {
    STATE_IDLE  = 0x0,      // Motors are stopped
    STATE_DRIVE = 0x1,      // Driving forward.
    STATE_PIVOT = 0x2,      // Pivoting in place.
    STATE_TRACK = 0x3,      // Tracking desired heading at speed
} state;


enum {
    RUDDER_TURN_NONE = 0x0,
    RUDDER_TURN_LEFT,   
    RUDDER_TURN_RIGHT, 
} rudderDirection, lastRudderDirection;


static uint8_t desiredSpeed = 0; // (percent) from 0 to 100%

static uint16_t desiredHeading = 0; // (degrees) from North

#ifdef USE_PUBLIC_DEBUG
char debugString[100];
#endif


/***********************************************************************
 * PRIVATE PROTOTYPES                                                  *
 ***********************************************************************/
static void startIdleState();
static void startDriveState();
static void startTrackState();
static void stopMotors();
static void setLeftMotor(uint8_t speed);
static void setRightMotor(uint8_t speed);
static void setRudder(char direction, uint8_t percentAngle);
static void updateRudder();


/***********************************************************************
 * PUBLIC FUNCTIONS                                                    *
 ***********************************************************************/

/**********************************************************************
 * Function: Drive_init
 * @return SUCCESS or FAILURE.
 * @remark Initializes the drive system state machine.
 * @author David Goodman
 * @date 2013.03.27 
 **********************************************************************/
bool Drive_init() {


    uint16_t RC_pins = MOTOR_LEFT  | MOTOR_RIGHT | RUDDER;
    RC_init(RC_pins);
    Timer_new(TIMER_DRIVE, 1);

#ifdef DEBUG
    // Timers for debug print statements
    Timer_new(TIMER_TEST2,1);
    Timer_new(TIMER_TEST3,1);
#endif

    state = STATE_IDLE;
}

   
/**********************************************************************
 * Function: Drive_runSM
 * @return None.
 * @remark Executes a cycle of the drive system state machine.
 * @author David Goodman
 * @date 2013.03.27 
 **********************************************************************/
void Drive_runSM() {
    switch (state) {
        case STATE_IDLE:
            // Do nothing
            break;
        case STATE_DRIVE:
            // Just driving, do nothing
            break;
        case STATE_TRACK:
            if (Timer_isExpired(TIMER_DRIVE)) {
                updateRudder();
                Timer_new(TIMER_DRIVE, TRACK_UPDATE_DELAY);
            }
            break;

    } // switch
}

/**********************************************************************
 * Function: Drive_forward
 * @return None
 * @param Speed to drive both motors forward in percent, from 0 to 100.
 * @remark Drives both motors at the given speed.
 * @author David Goodman
 * @author Darrel Deo
 * @date 2013.03.27 
 **********************************************************************/
void Drive_forward(uint8_t speed) {
    desiredSpeed = speed;

    // Start driving the given speed
    setLeftMotor(speed);
    setRightMotor(speed);

    startDriveState();
}

/**********************************************************************
 * Function: Drive_forwardHeading
 * @return None
 * @param Speed to drive at in meters per second.
 * @param Heading to hold in degrees from north, from 0 to 359.
 * @remark Tracks the given speed and heading.
 * @author David Goodman
 * @date 2013.03.30 
  **********************************************************************/
void Drive_forwardHeading(uint8_t speed, uint16_t angle) {
    desiredSpeed = speed;
    desiredHeading = angle;
    
    // Start driving the given speed
    desiredSpeed = speed;
    setLeftMotor(speed);
    setRightMotor(speed);

    // Let rudder controller steer us
    startTrackState();
}

/**********************************************************************
 * Function: Drive_stop
 * @return None
 * @remark Stops both motors from driving.
 * @author David Goodman
 * @author Darrel Deo
 * @date 2013.03.27 
 **********************************************************************/
void Drive_stop() {
    startIdleState();
}


/**********************************************************************
 * Function: Drive_getDebugString
 * @return None
 * @remark 
 * @author David Goodman
 * @date 2013.05.25 
 **********************************************************************/
char *Drive_getDebugString() {
    #ifdef USE_PUBLIC_DEBUG
    return debugString;
    #else
    return "";
    #endif
}


/*******************************************************************************
 * PRIVATE FUNCTIONS                                                          *
 ******************************************************************************/


/**********************************************************************
 * Function: startIdleState
 * @return None
 * @remark Switches into the idle state, which stops the boat.
 **********************************************************************/
static void startIdleState() {
    state = STATE_IDLE;
    desiredSpeed = 0;

    stopMotors();
}

/**********************************************************************
 * Function: startDriveState
 * @return None
 * @remark Switches into the drive state for driving straight forward.
 **********************************************************************/
static void startDriveState() {
    state = STATE_DRIVE;
}

/**********************************************************************
 * Function: startTrackState
 * @return None
 * @remark Switches into the track state for maintaining a heading
 *  and driving forward at a given speed.
 **********************************************************************/
static void startTrackState() {
    state = STATE_TRACK;
    //stopMotors();

    lastRudderDirection = RUDDER_TURN_NONE;
}

/**********************************************************************
 * Function: stopMotors
 * @return None
 * @remark Stops both motors from driving.
 **********************************************************************/
static void stopMotors() {
    setLeftMotor(0);
    setRightMotor(0);
}

/**********************************************************************
 * Function: setLeftMotor
 * @param Speed in percent from 0 to 100%.
 * @return None
 * @remark Sets the left motor to drive at the given speed in percent.
 **********************************************************************/
static void setLeftMotor(uint8_t speed) {
    uint16_t rc_time = MOTOR_PERCENT_TO_RCPULSE(speed);
    // Limit the rc times
    if (rc_time > RC_MOTOR_MAX)
        rc_time = RC_MOTOR_MAX;
    if (rc_time < RC_MOTOR_MIN)
        rc_time = RC_MOTOR_MIN;

    DBPRINT("Setting left motor to RC_TIME=%d\n",rc_time);
    #ifndef DISABLE_MOTORS
    RC_setPulseTime(MOTOR_LEFT, rc_time);
    #endif
}

/**********************************************************************
 * Function: setRightMotor
 * @param Speed in percent from 0 to 100%.
 * @return None
 * @remark Sets the right motor to drive at the given speed in percent.
 **********************************************************************/
static void setRightMotor(uint8_t speed) {
    uint16_t rc_time = MOTOR_PERCENT_TO_RCPULSE(speed);
    // Limit the rc times
    if (rc_time > RC_MOTOR_MAX)
        rc_time = RC_MOTOR_MAX;
    if (rc_time < RC_MOTOR_MIN)
        rc_time = RC_MOTOR_MIN;

    DBPRINT("Setting right motor to RC_TIME=%d\n",rc_time);
    #ifndef DISABLE_MOTORS
    RC_setPulseTime(MOTOR_RIGHT, rc_time);
    #endif
}

/**********************************************************************
 * Function: setRudder
 * @param Direction left or right to set the rudder to (0 = LEFT, 1 = RIGHT).
 * @param Angle in percent of full rudder range to set to (0 to 100%).
 * @return None
 * @remark Sets the right motor to drive at the given speed in percent.
 **********************************************************************/
static void setRudder(char direction, uint8_t percentAngle) {
    uint16_t rc_time = (direction == RUDDER_TURN_LEFT)?
        RUDDER_PERCENT_TO_RCPULSE_LEFT(percentAngle)
        :
        RUDDER_PERCENT_TO_RCPULSE_RIGHT(percentAngle);

    // Limit the rc times
    if (rc_time > RC_RUDDER_MAX)
        rc_time = RC_RUDDER_MAX;
    if (rc_time < RC_RUDDER_MIN)
        rc_time = RC_RUDDER_MIN;

    DBPRINT("Setting rudder to RC_TIME=%d\n",rc_time);
    RC_setPulseTime(RUDDER, rc_time);
}

// ---------------- Update functions for state machines ---------------

/**********************************************************************
 * Function: updateHeading
 * @return None
 * @remark Determines the heading error using the tilt-compensated compass,
 *  and adjusts the rudder accordingly. Also, a bang-bang control has been
 *  implemented to turn the rudder to the maximum value if the boat's motors
 *  are being driven below some percentage defined above.
 * @author Darrel Deo
 * @author David Goodman
 * @date 2013.03.27 
 **********************************************************************/
static void updateRudder() {

    static int16_t lastThetaError; // used for derivative term
    
    rudderDirection = RUDDER_TURN_LEFT;
    
    // Get current heading, determine theta error
    uint16_t currentHeading = (uint16_t)TiltCompass_getHeading();
    int16_t thetaError = desiredHeading - currentHeading;
    
    // Bound theta error and determine turn direction
    if (thetaError > 0) {
        rudderDirection = (thetaError < 180)? RUDDER_TURN_RIGHT : RUDDER_TURN_LEFT;
        thetaError = (thetaError < 180)? thetaError : (360 - thetaError);
    }
    else {
        // theta error is negative
        rudderDirection = (thetaError > -180)? RUDDER_TURN_LEFT : RUDDER_TURN_RIGHT;
        thetaError = (thetaError > -180)? -thetaError : (360 + thetaError);
    }
    
    // Initialize or dump derivative if changed directions
    if (lastRudderDirection == RUDDER_TURN_NONE || rudderDirection != lastRudderDirection)
        lastThetaError = 0;
        
    /*    Controller Terms    */
    // Derivative (scaled by KD_RUDDER)
    float thetaErrorDerivative = (float)abs(thetaError - 
        lastThetaError)/MS_TO_SEC(TRACK_UPDATE_DELAY);
    
    // Proportional (scaled by KP_RUDDER), convert degrees to percent
    float uDegrees = KP_RUDDER*(float)thetaError + KD_RUDDER*thetaErrorDerivative;
    float uPercent = (uDegrees / RUDDER_ANGLE_MAX ) * 100;
    
    // Limit percentage from 0 to 100
    uPercent = (uPercent > 100.0)? 100.0f : uPercent;
    uPercent = (uPercent < 0.0)? 0.0f : uPercent;

    char *bangbang = "";
    // Bang-bang control to force rudder all the way if speed is low
    if (desiredSpeed < RUDDER_BANGBANG_SPEED_THRESHOLD
            && thetaError > RUDDER_BANGBANG_THETA_DEADBAND_THRESHOLD) {
        uPercent = 100.0f;
        bangbang = " BB";
    }
    
    // Command the rudder and save 
    setRudder(rudderDirection, (uint8_t)uPercent);
    lastThetaError = thetaError;
    lastRudderDirection = rudderDirection;
    char *dir;
    dir = (rudderDirection == RUDDER_TURN_RIGHT)? "R" : "L";
        
    #ifdef DEBUG_VERBOSE
    DBPRINT("Rudder control: rDegrees=%d, yDegrees=%d, eDegrees=%d, uDegrees=%.2f, uPercent=%d[%s]\n\n",
        desiredHeading, currentHeading, thetaError, uDegrees, (uint8_t)uPercent, dir);
    #endif

    #ifdef USE_PUBLIC_DEBUG
    sprintf(debugString, "R=%d, Y=%d, e=%d, U=%.2f, Up=%d[%s]%s, S=%d\n",
        desiredHeading, currentHeading, thetaError, uDegrees, (uint8_t)uPercent, dir, bangbang, desiredSpeed);
    #endif
}



/***********************************************************************
 * TEST HARNESSES                                                      *
 ***********************************************************************/

//#define DRIVE_TEST
#ifdef DRIVE_TEST

#define TEST_DELAY      2000 // (ms)

int main() {
    enum{
        forward =  0x01,
        backward = 0x02,
        idle    =  0x03,
    }drive_state;

    Board_init();
    Serial_init();
    Timer_init();
    Drive_init();
    int spd = 20;
    //Magnetometer_init();
    printf("Boat initialized.\n");
    Drive_forward(spd);
    Timer_new(TIMER_TEST,TEST_DELAY);
    drive_state = forward;
    int flag = 0;
    while (1) {
        switch(drive_state){
            case forward:
                Drive_forward(spd);
                if(Timer_isExpired(TIMER_TEST)){
                    drive_state = idle;
                    Drive_stop();
                    Timer_new(TIMER_TEST,TEST_DELAY);
                    flag = 0;
                }
                break;
            case idle:
                Drive_stop();
                if(Timer_isExpired(TIMER_TEST)){
                    if (flag == 0){
                        drive_state = backward;
                        Drive_backward(spd);
                    }else if (flag == 1){
                        drive_state = forward;
                        Drive_forward(spd);
                    }
                    Timer_new(TIMER_TEST,TEST_DELAY);
                }

                break;
            case backward:
                Drive_backward(spd);
                if(Timer_isExpired(TIMER_TEST)){
                    drive_state = idle;
                    Drive_stop();
                    Timer_new(TIMER_TEST,TEST_DELAY);
                    flag = 1;
                }
        }

            Drive_runSM();

    }

    Drive_stop();
    Drive_runSM();

    return SUCCESS;
}

#endif

//#define PIVOT_TEST_DRIVE
#ifdef PIVOT_TEST_DRIVE
//#define MOTOR_TEST
#define RUDDER_TEST
#define MICRO 0

#define FINISH_DELAY      5000 // (ms)
#define ENABLE_OUT_TRIS  PORTX12_TRIS // J5-06
#define ENABLE_OUT_LAT  PORTX12_LAT // J5-06, //0--> Microcontroller control, 1--> Reciever Control

I2C_MODULE      I2C_BUS_ID = I2C1;
// Set Desired Operation Frequency
#define I2C_CLOCK_FREQ  80000 // (Hz)

int main() {
    ENABLE_OUT_TRIS = OUTPUT;            //Set Enable output pin to be an output, fed to the AND gates
    ENABLE_OUT_LAT = MICRO;             //Initialize control to that of Microcontroller
    Board_init();
    Serial_init();
    Timer_init();
    Drive_init();
    I2C_init(I2C_BUS_ID, I2C_CLOCK_FREQ);
    TiltCompass_init();
    printf("Boat initialized.\n");

    Drive_stop();
    DELAY(5);
#ifdef MOTOR_TEST
    Drive_pivot(0);
#endif

#ifdef RUDDER_TEST
   Drive_forwardHeading(0.0, desiredHeading);
#endif
   int i = 0;
   int velocity[] = {1600, 1600, 1600, 1600, 1600};
   velocityPulse = velocity[i];
    Timer_new(TIMER_TEST,FINISH_DELAY);
    while (1) {
        if (Timer_isExpired(TIMER_TEST))
        {
            i++;
            if (i == 5){
                i = 0;
            }
            velocityPulse = velocity[i];
           printf("CURRENT VELOCITY: %d\n\n",velocityPulse);
            Timer_new(TIMER_TEST,FINISH_DELAY);

        }
         
        Drive_runSM();
        TiltCompass_runSM();
    }

    Drive_stop();

    return SUCCESS;
}

#endif


//#define RECIEVER_OVERRIDE_TEST
#ifdef RECIEVER_OVERRIDE_TEST

//Define the Enable input pin which should  be interrupt driven in the future.
#define ENABLE_TRIS  PORTX10_TRIS // 0--> Output    1-->Input, J5-08
#define ENABLE_BIT  PORTX10_BIT // 0--> Low 0     1-->HIGH 1 J5-08

#define ENABLE_OUT_TRIS  PORTX12_TRIS // J5-06
#define ENABLE_OUT_LAT  PORTX12_LAT // J5-06, //0--> Microcontroller control, 1--> Reciever Control

#define RECIEVER_DELAY      3000 // (ms)
#define MICRO 0
#define RECIEVER 1
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
int main(){
    //Initializations
    Board_init();
    Serial_init();
    Timer_init();
    if (Drive_init() != SUCCESS) {
        printf("Failed to initialize drive module.\n");
    }
    I2C_init(TILT_COMPASS_I2C_ID, I2C_CLOCK_FREQ);
    if (TiltCompass_init() != SUCCESS) {
        printf("Failed to initialize tilt compass module.\n");
    }
    ENABLE_OUT_TRIS = OUTPUT;

    while (1) {
        printf("Driving north at full speed.\n");
        Timer_new(TIMER_TEST, COMMAND_DELAY);
        Drive_forwardHeading(100, 0);

        while(!Timer_isExpired(TIMER_TEST)) {
            //wait for finish
            DELAY(1);
            Drive_runSM();
            TiltCompass_runSM();
        }
        Drive_stop();
        Drive_runSM();
        TiltCompass_runSM();

        printf("Driving south at full speed.\n");
        Timer_new(TIMER_TEST, COMMAND_DELAY);
        Drive_forwardHeading(100, 180);

        while(!Timer_isExpired(TIMER_TEST)) {
            //wait for finish
            DELAY(1);
            Drive_runSM();
            TiltCompass_runSM();
        }
        
        Drive_stop();
        Drive_runSM();
        TiltCompass_runSM();
        delayMillisecond(COMMAND_DELAY);
        printf("Waiting for retry...\n");

    }

    return SUCCESS;
}


#endif

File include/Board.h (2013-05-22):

/**
 * @file    Board.h
 * @author  Max Dunne
 * @author  David Goodman
 *
 * @brief
 * Interface for PIC32 board.
 *
 * @details
 * Contains functions and definitions for a PIC32 board.
 *
 * 
 * @date January 1, 2013            -- Edited
 * @date December 19, 2012, 2:08 PM -- Created
 */

//#define DEBUG

#ifndef Board_H
#define	Board_H

#include <xc.h>
#include <plib.h>
#include <stdarg.h>
#include <stdint.h>
#include <stdbool.h>
#include "Serial.h"
#include "Error.h"
#include "Timer.h"
#include "LCD.h"

#ifdef USE_SD_LOGGER
#include "Logger.h"
#endif

/*******************************************************************************
 * PUBLIC #DEFINES                                                             *
 ******************************************************************************/

#define DELAY(ms)   do { int i; for (i = 0; i < (ms << 8); i++) { asm ("nop"); } } while(0);

#define MS_TO_SEC(ms)  ((float)ms/1000)

// Debugging statements over terminal, SD logger, or disabled (respectively)
/*
#ifdef DEBUG
#ifdef USE_SD_LOGGER
//#define DBPRINT(...)   do { char debug[255]; sprintf(debug,__VA_ARGS__); } while(0)
#else
//#define DBPRINT(...)   printf(__VA_ARGS__)
#endif
#else
*/
#define DBPRINT(...)   ((int)0)
//#endif

/*****************************************************************************/
// Boolean defines for TRUE, FALSE, SUCCESS and ERROR
#ifndef TRUE
#define FALSE ((int8_t) 0)
#define TRUE ((int8_t) 1)
#endif

#ifndef ERROR
#define ERROR ((int8_t) -1)
#endif

#ifndef SUCCESS
#define SUCCESS ((int8_t) 0)
#define FAILURE ((int8_t) 1)
#endif

#ifndef OUTPUT
#define OUTPUT  (0)
#define INPUT   (1)
#endif

#ifndef ON
#define ON      (1)
#define OFF     (0)
#endif

// Timer allocation
#define TIMER_BAROMETER         1
#define TIMER_ACCELEROMETER     2
#define TIMER_THERMAL           3
#define TIMER_GPS               4
#define TIMER_ENCODER           5
#define TIMER_BUTTONS           6
#define TIMER_DRIVE             7
#define TIMER_OVERRIDE          8
#define TIMER_TILTCOMPASS       9
#define TIMER_NAVIGATION        10
#define TIMER_LOGGER            11
#define TIMER_BAROMETER2        12 // remove the blocking code!!
#define TIMER_DELAY             13
#define TIMER_INTERFACE         14
#define TIMER_LIGHT_HOLD        15
#define TIMER_LCD_HOLD          16
#define TIMER_I2C_TIMEOUT       17
#define TIMER_RESET             18
#define TIMER_INIT              19

// Master state machine timers
#define TIMER_MAIN              23
#define TIMER_MAIN2             24
#define TIMER_MAIN3             25
#define TIMER_BACKGROUND        26
#define TIMER_BACKGROUND2       27
#define TIMER_BACKGROUND3       28

// test harness timers
#define TIMER_TEST              29
#define TIMER_TEST2             30
#define TIMER_TEST3             31


#ifdef Board_H_PRIVATE_INCLUDE

/*
 LED5 => #58 => RA2
 */
#define BOARD_LED1_TRIS
#define BOARD_LED2_TRIS
#define BOARD_LED3_TRIS
#define BOARD_LED4_TRIS
#define BOARD_LED5_TRIS

#define BOARD_LED1_LAT
#define BOARD_LED2_LAT
#define BOARD_LED3_LAT
#define BOARD_LED4_LAT
#define BOARD_LED5_LAT

#endif


// Options
#define USE_SERIAL      0x1
#define USE_LCD         0x2
#define USE_TIMER       0x4

/*******************************************************************************
 * Public Functions                                                            *
 ******************************************************************************/
/**
 * Function: Board_init
 * @return None.
 * @remark Initializes the Serial interface and enables interrupts.
 * @author David Goodman
 * @date 2013.01.18  */
void Board_init();

void Board_configure(uint8_t opts);

/**
 * Function: Board_GetPBClock
 * @return System bus speed in hertz.
 * @author David Goodman
 * @date 2013.01.18  */
uint32_t Board_GetPBClock();

/**
 * Function: delayMillisecond
 * @param Number of millisecond to delay.
 * @return None
 * @remark Blocking delay using timer module.
 * @author David Goodman
 * @date 2013.04.11  */
void delayMillisecond(int ms);

void dbprint(char *fmt, ...);



#endif	/* Board_H */

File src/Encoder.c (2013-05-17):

/* 
 * File:   Encoder_I2C.c
 * Author: Shehadeh
 *
 * Created on January 21, 2013, 11:52 AM
 */
//#define DEBUG

#include <xc.h>
#include <stdio.h>
#include <plib.h>
#include <math.h>
#include "I2C.h"
#include "Serial.h"
#include "Board.h"
#include "Ports.h"
#include "Encoder.h"
#include "Timer.h"


/***********************************************************************
 * PRIVATE DEFINITIONS                                                 *
 ***********************************************************************/
// List of registers for Encoder
#define SLAVE_PITCH_READ_ADDRESS      0x81
#define SLAVE_PITCH_WRITE_ADDRESS     0x80
#define SLAVE_YAW_READ_ADDRESS        0x87
#define SLAVE_YAW_WRITE_ADDRESS       0x86

#define READ_SLAVE_ADDRESS            0x15
#define READ_ANGLE_ADDRESS            0xFE
#define READ_DIAGNOSTIC_ADDRESS       0xFB

#define IS_OCF_SET(byte)            (0x1 & byte) // should return 1 if calibrated

#define ENCODER_RESOLUTION          14 // (bits)
#define MAX_ENCODER_NUMBER          (1<<ENCODER_RESOLUTION) // (encoder counts)
#define DEGREE_PER_NUMBER           ((float)360.0f / MAX_ENCODER_NUMBER)
//#define DEGREE_PER_NUMBER           (0.02197265625f)

// Raw angle hysteresis for low/high edge selection
#define DELTA_DEGREE      2.5f // (degree) width of hysteresis for choosing sides
#define MIN_DEGREE    0.0f // (degree) minimum measured
#define MAX_DEGREE    360.0f // (degree) max measured

#define STARTUP_STRAP_DELAY        100 //(ms) to finish offset compensation

#define ACCUMULATOR_LENGTH  150


/***********************************************************************
 * PRIVATE VARIABLES                                                   *
 ***********************************************************************/
// Pick the I2C_MODULE to initialize
I2C_MODULE      ENCODER_I2C_ID = I2C1;
// Set Desired Operation Frequency
#define I2C_CLOCK_FREQ  50000 // (Hz)

// Set Desired Operation Frequency
//#define I2C_CLOCK_FREQ  100000 // (Hz)

// Measured encoder angles
float pitchAngle = 0.0; // (degrees) calculated angle
float yawAngle = 0.0; // (degrees) calculated angle

// Calibration related
float zeroPitchAngle = 0.0; // (degrees)
float zeroYawAngle = 0.0; // (degrees)
bool useZeroPitchAngle, useZeroYawAngle;

// Accumulator related
bool accumulateOnLowEdge;
bool accumulatePitch;
uint16_t accumulatorIndex;
float angleAccumulator = 0.0; // (degrees) accumlated angles

// Currently selected encoder variables
float currentZeroAngle;
uint16_t currentReadAddress;
uint16_t currentWriteAddress;

/***********************************************************************
 * PRIVATE PROTOTYPES                                                  *
 ***********************************************************************/

static uint16_t readDevice(uint8_t deviceReadAddress, uint8_t deviceWriteAddress, uint8_t dataAddress);
static void choosePitchEncoder();
static void chooseYawEncoder();
static void accumulateAngle(uint8_t deviceReadAddress, uint8_t deviceWriteAddress);
static float calculateAngle();

/***********************************************************************
 * PUBLIC FUNCTIONS                                                    *
 ***********************************************************************/


 void Encoder_runSM() {

     if (accumulatorIndex < ACCUMULATOR_LENGTH) {
        accumulateAngle(currentReadAddress, currentWriteAddress);
        accumulatorIndex++;
     }
     else {
        // calculate and switch encoder choice, resetting index
         calculateAngle();
     }
 }

char Encoder_init() {
    useZeroPitchAngle = FALSE;
    useZeroYawAngle = FALSE;

    choosePitchEncoder();

    DELAY(STARTUP_STRAP_DELAY);  // wait for start up compensation straps
    
    // Read from encoders to ensure they work
    /*
    uint8_t pitchDiagnostics = readDevice(SLAVE_PITCH_READ_ADDRESS, SLAVE_PITCH_WRITE_ADDRESS,
            READ_DIAGNOSTIC_ADDRESS);
    if (!IS_OCF_SET(pitchDiagnostics)) {
        DBPRINT("Encoder: pitch offset compensation failed (0x%X).\n", pitchDiagnostics);
        return FAILURE;
    }
    uint8_t yawDiagnostics = readDevice(SLAVE_YAW_READ_ADDRESS, SLAVE_YAW_WRITE_ADDRESS,
            READ_DIAGNOSTIC_ADDRESS);
    if (!IS_OCF_SET(yawDiagnostics)) {
        DBPRINT("Encoder: yaw offset compensation failed (0x%X).\n", yawDiagnostics);
        return FAILURE;
    }
    */
    if (I2C_hasError())
        return FAILURE;
    
    return SUCCESS;
}

void Encoder_setZeroPitch() {
    zeroPitchAngle = pitchAngle;
    useZeroPitchAngle = TRUE;
}


void Encoder_setZeroYaw() {
    zeroYawAngle = yawAngle;
    useZeroYawAngle = TRUE;
}
    
float Encoder_getPitch() {
    return pitchAngle;
}

float Encoder_getYaw() {
    // Invert yaw direction to be CW from north
    return 360.0f - yawAngle;
}



/******************************************************************************
 * PRIVATE FUNCTIONS                                                          *
 ******************************************************************************/

static void choosePitchEncoder() {
    currentZeroAngle = zeroPitchAngle;
    currentReadAddress = SLAVE_PITCH_READ_ADDRESS;
    currentWriteAddress = SLAVE_PITCH_WRITE_ADDRESS;
    angleAccumulator = 0.0;
    accumulatorIndex = 0;
    accumulatePitch = TRUE;
}

static void chooseYawEncoder() {
    currentZeroAngle = zeroYawAngle;
    currentReadAddress = SLAVE_YAW_READ_ADDRESS;
    currentWriteAddress = SLAVE_YAW_WRITE_ADDRESS;
    angleAccumulator = 0.0;
    accumulatorIndex = 0;
    accumulatePitch = FALSE;
}

static void accumulateAngle(uint8_t deviceReadAddress, uint8_t deviceWriteAddress) {
   float rawAngle = readDevice(deviceReadAddress, deviceWriteAddress, READ_ANGLE_ADDRESS) * DEGREE_PER_NUMBER;

   
   // Decide which edge to stay on
   if (accumulatorIndex == 0) {
       accumulateOnLowEdge = (rawAngle <= (MIN_DEGREE + DELTA_DEGREE))?
           TRUE : FALSE;
   }
   
   // Did we start on 0 side, and teetered over to 360 side?
   if (accumulateOnLowEdge && (rawAngle >= (MAX_DEGREE - DELTA_DEGREE)))
       rawAngle -= MAX_DEGREE; // makes it negative

   // Did we start on 360 side and teetered over to the 0 side?
   if (!accumulateOnLowEdge && (rawAngle <= (MIN_DEGREE + DELTA_DEGREE)))
       rawAngle += MAX_DEGREE;
    
    /*
   if  (accumulateOnLowEdge && (rawAngle <= MAX_DEGREE && rawAngle >= (MAX_DEGREE - DELTA_DEGREE))
           || !accumulateOnLowEdge && (rawAngle >=  MIN_DEGREE && rawAngle <= (MIN_DEGREE + DELTA_DEGREE)))
       rawAngle = 0.0f;
   */
   angleAccumulator += rawAngle;

}
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

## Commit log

2012-12-28 Initial commit.
    [3DR-GPS-LEA6-JST-v11-RELEASE.brd, 3DR-GPS-LEA6-JST-v11-RELEASE.sch, ElectricRCBoats.xlsx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]
2013-01-05 Added notes, refs, datasheets, examples folder, images, financial docs, and updated gps model functions.
    [encoder_uncertainty.xlsx]
2013-01-17 Finalized kresge proposal cover sheet, budget, and letters of rec.
    [itemized_budget.xlsx]
2013-01-19 I2C module Header and C File. Implemented Start, Stop, Send Byte.
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2013-01-19 Included the First iteration of the UART code. We still need to test the code and guarantee that it is working properly.
    I also deleted a file that I believe was causing errors. It was 0 bytes, and the folder said that it had been modified, when it had not.
    [Uart.c]
2013-01-19 These are my initial Xbee Files. I believe these are all the files I will need.
    Now that Uart.c is started I can begin implementing the correct functions into the Xbee.c. There will be updated again in the next few days.
    [Xbee.c]
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2013-01-25 Reformatted itemized budget. Added thermal MATLAB code, and added data sheets.
    [itemized_budget.xlsx, power_budget.xlsx]
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2013-01-30 Finished 2D scatter plot with stats. Ready for extensive GPS tests.
    [test.csv]
2013-02-03 Many changes code and documents. Renamed I2C to Barometer project, added gps data and plots, modified barometer and i2c modules, and many other changes.
2013-02-08 Added GPS code, updated doxygen, added gps data plots, modified Board and Serial modules.
2013-02-09 Completed GPS code (still bugs) and updated test data.
    [test.csv]
2013-02-10 Solidworks for command center and boat initiated.
    [AtLAs.SLDPRT, Encoder Mounts.SLDDRW, Pitch Arm.SLDPRT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]
2013-02-10 Finished GPS lat,lon,alt code. Still need velocity and error setting.
    [Gps.c]
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2013-02-11 Encoder code that dumps angle value through serial. No running avg. implemented yet.
2013-02-13 Added serial logging tool and miniterm.
    Next comes py2exe and some fine tuning for serial_logger.
    [.config.cfg]
2013-02-13 Small fixes to Xbee Test and #defines
    [Xbee.c]
2013-02-14 Added serial logger. Has one error.
    Unexplainable error showing up in data character from serial.read(1):
    Error: Sent byte was not acknowledged
    [serial_logger.py]
2013-02-14 Fixed bug of measuring positive and negative pulsewidth in test harness. Need to fix for actual SM.
    [Encoder.c]
2013-02-14 Thermal,baro,and solidworks changes.
    [Pitch Disk.SLDPRT, Pitch Mount no hole.sldprt, Pitch Mounts.sldprt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]
2013-02-15 MATLAB code that outputs pixels in the appropriate orientation. Set up for 4Hz.
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2013-02-17 Finished gui, but one bug crashes.
    [serial_logger_gui.py]
2013-02-17 Possibly fixed crashing. Added file menus and removed locks.
    [serial_logger_gui.py]
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2013-02-23 Finished gui and packed in exe for win.
    Need mac app, and need icon in tkinter.
    [encoder_uncertainty.xlsx]
2013-02-23 Added LCD datasheet and renamed encoder uncertainty to old.
    [encoder_uncertainty_old.xlsx]
2013-02-23 Finished non-bundles serial_logger, and fixed gps record test to be more robust.
    [serial_logger_gui.py]
2013-02-25 Broken Sonar, about to create a new project.
2013-02-25 Sonar Compiling, and getting proper data. Analog window does not seem to be working.
2013-02-26 Sonar working getting data in the correct way.
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2013-03-01 Added GPS error correction code to pic, and MATLAB test.
    [Gps.c]
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2013-03-09 Moved position into Compas project. Fixed up Encoder module.
    [Accelerometer.c, Barometer.c, Compas.c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]
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2013-03-10 Solidworks and Xbee Circuits
    [AtLAs.SLDPRT, Box top.SLDDRW, Box top.SLDPRT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]
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2013-03-10 Proper placement of solidworks and schematics
    [AtLAs.SLDPRT, Box top.SLDDRW, Box top.SLDPRT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]
2013-03-10 Added Magnetometer.h, fixed heading calculation. Improved command center.
    [Accelerometer.c, Compas.c, Encoder.c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]
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2013-03-10 Fixed GPS project, added Navigation, fixed COMPAS.
    [Compas.c, Gps.c, Navigation.c]
2013-03-14 Not compiling, Errors with navigation and Magnetometer functions
    [Compas.c, Xbee.c]
2013-03-14 Fixed navigation NED calculations.
    [Compas.c, Navigation.c]
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2013-03-15 Command center working. Fixed Xbee timer #.
    [Board.h, Compas.c, Xbee.c]
2013-03-23 New Schematics and Mavlink changes to print f
    [PTN78000.brd, PTN78000.sch, Xbee circuit.sch]
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2013-03-27 Encoder model and ComPAS schematics.
    [accelerometer_level.sch]
2013-03-27 updateHeading function implemented, Controller implemented digitally and Ucmd is utilized in a 1:3 ratio when governing PWM duty cycles for differential motor drive
2013-03-27 Wrote updateHeading for Drive module.
    updateHeading function implemented, Controller implemented digitally and Ucmd is utilized in a 1:3 ratio when governing PWM duty cycles for differential motor drive
2013-03-29 Updated the updateHeading so that it normalizes the pwm signal so that we may scale it accordingly for any actuator
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2013-03-29 Command Center box finished
    [Bottom.SLDPRT, Box.SLDASM, Long Side.SLDPRT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]
2013-03-30 Updated the DRIVE_TEST harness because initial RC_SERVO pins did not work, I also altered it to work as a state machine to move the motors backwards and forwards. I created my own test harness that t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
    [Board.h, Drive.c]
2013-03-31 Atlas power management schematic.
    [ATLAS_POWER.DSN]
2013-03-31 Started the barometer message, hit a strange error.
    [Xbee circuit.brd, Xbee circuit.sch]
2013-03-31 Changed color and took a picture of the render
    [Bottom.SLDPRT, Box.SLDASM, Long Side.SLDPRT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]
2013-03-31 Xbee Schematics, created Gerber Files. I do not believe they work.
    [Xbee circuit.GBL, Xbee circuit.GBO, Xbee circuit.GBS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]
2013-04-01 Updated UpdateHeading so that it uses floats to properly read the float angle coming out of the magnetometer for heading. Mangetometer.c was changed so that the accumulator is now 1 in order for aver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
    [Drive.c, Magnetometer.c]
2013-04-02 Implemented a new test harness which uses an interrupt driven protocol to handle the hand-off between the Micro and Reciever for control. ISR function is included as well as an Override_init which in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
2013-04-05 Schematics: XBEE finished, Compas Started Power supply: looked at.
    [Xbee circuit.brd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]
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2013-04-08 merged rudder init with drive init and changed some test harnesses to test rudder control. It works fine.
2013-04-08 Schematics fixed
    [PTN78000.sch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]
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2013-04-12 New schematics
    [ATLAS_POWER.DSN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]
2013-04-12 Improved rudder controller to use velocity as a scalar for actuator effort. Also, if the boat flips around 180 degrees off of its desired point, it will continue to turn in a direction until it reach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
    [Drive.c]
2013-04-12 Fixed GPS course heading, and nav. test ready.
    [Gps.c, Navigation.c]
2013-04-12 Fixed Precision, and added a new test.
    [Barometer.c]
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2013-04-13 Fixed tilt compass offset calculations.
    [TiltCompass.c]
2013-04-15 Schematic updates
    [PTN78000.brd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]
2013-04-15 Added waterproof box
    [Board.SLDPRT, Bottom.SLDPRT, Box.SLDASM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]
2013-04-21 Completed CC box below.
    [Bottom.SLDPRT, Box.SLDASM, CC Box.slddrw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]
2013-04-21 Cleaned up the XBee circuit
    [Xbee circuit.GBL, Xbee circuit.GBO, Xbee circuit.GBS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]
2013-04-22 Started reworking the drive module.
    [Drive.c]
2013-04-22 Nice looking L shape
    [Bottom.SLDPRT, Box.SLDASM, Inside L.SLDPRT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]
2013-04-23 Updated L with individual parts
    [Bottom.SLDPRT, Box.SLDASM, Inside L.SLDPRT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]
2013-04-27 Mavlink, barometer, and error changes. Ready for John.
    [Barometer.c]
2013-04-27 Updated Solidworks model from git hub
    [Bottom.SLDPRT, Box.SLDASM, Inside L.SLDPRT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]
2013-04-27 * Regenerate from XML * Write code for function headers I put in Mavlink.h (see -Message Status Codes-, I wrote one in Mavlink.c as an example). Also, functions with no ack arguments are assumed ack=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
2013-04-27 Replaced BOOL with bool from stdbool.h, plus Atlas changes.
    [Atlas.c, Barometer.c, Compas.c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]
2013-04-29 Latest Solidwork changes from Drop Box on 4.28.2013
    [Bottom.SLDPRT, Box.SLDASM, Inside L.SLDPRT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]
2013-04-29 XBEE schematic cleaned up, I/O board added from drop box 4/28/2013
    [IO Shield.brd, IO Shield.sch, IO Shield_With_Power_Supply.brd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]
2013-05-04 Quick changes to modules. Added old accelerometer schematic.
    [LCD.DSN, ACCELEROMETER_LEVEL.DSN]
2013-05-04 Changes to LCD schematic.
    [LCD.DSN]
2013-05-05 Finished SM and working on GPS fixes.
    [Atlas.c, Compas.c, Interface.c]
2013-05-05 Added GPS error correction code. Fixed Matlab tests.
    [Atlas.c, Compas.c, Navigation.c]
2013-05-05 Fixed AtLAs errors except ERROR_MESSAGE related
    [Atlas.c, Board.h, Navigation.c]
2013-05-11 Fixed Magnetometer negative.
2013-05-11 Fixed interface and enabled magnetometer test.
    [Interface.c, Magnetometer.c]
2013-05-12 Debugging ComPAS.
    Initialization succeeded, GPS read failed:
    Initializing magnetomer.
    Initializing encoder.
    Initializing accelerometer.
    Initializing GPS.
    Intializing the GPS on uart 2.
    Initializing XBee.
    Initializing barometer.
    Initializing interface.
    ComPAS initialized.
    Failed reading GPS message at byte 0.
    Failed reading GPS message at byte 0.
    [Compas.c, Encoder.c]
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2013-05-14 Merged in Johns physical design changes.
    [ACCELEROMETER_LEVEL.DSN, Arduino UNO.SLDPRT, Bottom.SLDPRT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]
2013-05-18 Added reset button. Fixed LCD bug in Board module.
    [Board.h, Compas.c, Interface.c]
2013-05-18 Made reset functions static.
    [Compas.c]
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2013-05-21 Atlas ready without GPS. Compas reset light feature.
    [Atlas.c, Board.h, Compas.c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]
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

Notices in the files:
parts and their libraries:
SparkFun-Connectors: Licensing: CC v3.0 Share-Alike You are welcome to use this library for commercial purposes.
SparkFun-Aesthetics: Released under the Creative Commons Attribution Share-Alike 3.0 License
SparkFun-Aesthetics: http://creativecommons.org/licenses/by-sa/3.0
